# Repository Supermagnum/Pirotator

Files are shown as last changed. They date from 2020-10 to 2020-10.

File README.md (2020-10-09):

# PiRotator #
This is cloned with permission from:
Ville Jussila (wilho / OH8ETB)

This is the rewritten code for raspberrypi based antenna rotator.
See more of project: https://jkry.org/ouluhack/PiRotator

### How do I get set up? ###

* You should get familiar with the code, most things should be pretty selfexplainig
* fill / modify paramaters in the code (pins,ttys, ip:s, speed, etc)
* Try / Error

### Disclaimer ###

 Ville Jussila (wilho / OH8ETB)
 https://jkry.org/ouluhack/pirotator
 
 Free as a free beer or something.. 
 use and do what ever you want, i will be pleased if you mention me on credits.

----------------------------------------------------------------------------
My personal notes and ideas:

It could use:
2X PicoBorg Reverse - Dual 5A Motor Controller ( already supported in the code )

https://www.piborg.org/motor-control-1135/picoborgrev

Or:
Adafruit DC & Stepper Motor Bonnet

https://www.adafruit.com/product/4280

----------------------------------------------------------------------------

1x Ozzmaker BerryGPS-IMU V3 

https://ozzmaker.com/product/berrygps-imu/

----------------------------------------------------------------------------

1X Adafruit LSM6DS33 + LIS3MDL - 9 DoF IMU with Accel / Gyro / Mag

https://www.adafruit.com/product/4485

----------------------------------------------------------------------------

1X Adafruit ADS1115 16-Bit ADC - 4 Channel with Programmable Gain Amplifier

https://thepihut.com/products/adafruit-ads1115-16-bit-adc-4-channel-with-programmable-gain-amplifier

----------------------------------------------------------------------------

Using the BerryGPS-IMU's onboard GPS should permit the raspberry Pi to know its geographic location, that is useful for those who are running mobile setups as that could be used in the calculations of where to point the antennas. It can also detect magnetic north. It will also detect if the mobile setups main mast is not 100% alligned to the "up" or X axis, and can be used to compensate for that if its not perfetcly straight up.
The Adafruit LSM6DS33's IMU can be used to detect the azimuth and elevation of the antennas mounting axle,its movement speed and where it is pointing related to North.

All the part above can communicate using a I2C bus which are supported in the code,in respect to the Borgpi stepper board. Magnetometer and GPS support is apparently not supported in the code.
Neither is "level compensation" .

The suggested features is explained in this picture:

https://github.com/Supermagnum/Pirotator/blob/main/axis.png

-----------------------------------------

It should be possible to supply DC voltages over the Coax cable using:

https://github.com/Supermagnum/Mjollnir

--------

I have made technical drawings for a sturdy aluminium insert that fits a Waterproof ABS box made by Fibox.
Its Product nbr: is 5330372
EAN: 6418074005540
http://www.fibox.com/catalog/135/product/862/5330372_ENG3.html

It has mouting holes for bolts that holds 2X Nema23 Stepper Motors 1.1Nm L56mm 3A + RV30 Worm Reducer gearbox.
Those are frequently found on Ebay, with a nice axle included.
It is to be made of aluminium, aircraft type. Some TIG or MIG welding, drilling of holes and milling is required.

PDF files for manufacturing,with drawings and assembly is located here:

https://github.com/Supermagnum/Pirotator/tree/main/mechanical-hardware

That also includes the Freecad file used to make the drawings.
The adapters that goes on the axles needs to be drilled as you feel fit, and needs a M5 or M6 bolt to stay put on the axle.

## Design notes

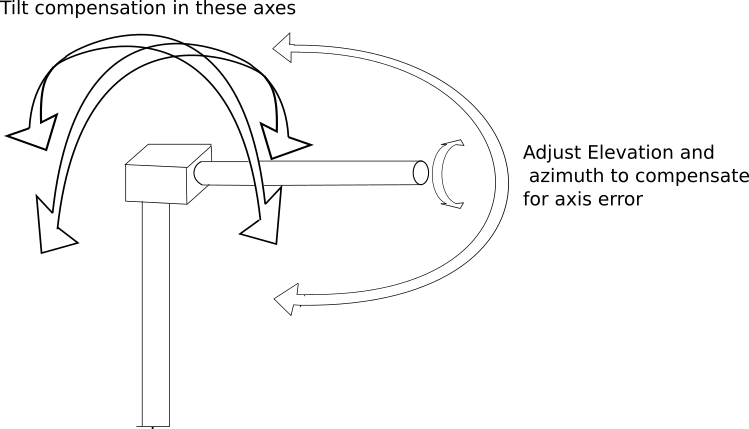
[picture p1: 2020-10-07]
axis.png

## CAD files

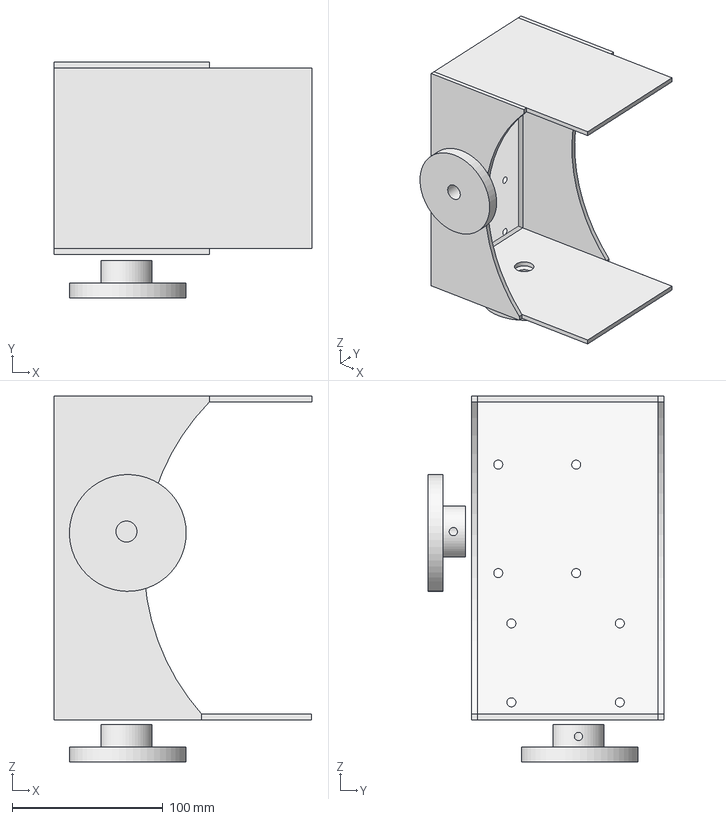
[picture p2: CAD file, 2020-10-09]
mechanical-hardware/az-el-rotor.FCStd
171.1 x 157.0 x 243.0 mm
top-plate
bottom-plate
adapter
sideplate1
sideplate002
back-plate
adapter001

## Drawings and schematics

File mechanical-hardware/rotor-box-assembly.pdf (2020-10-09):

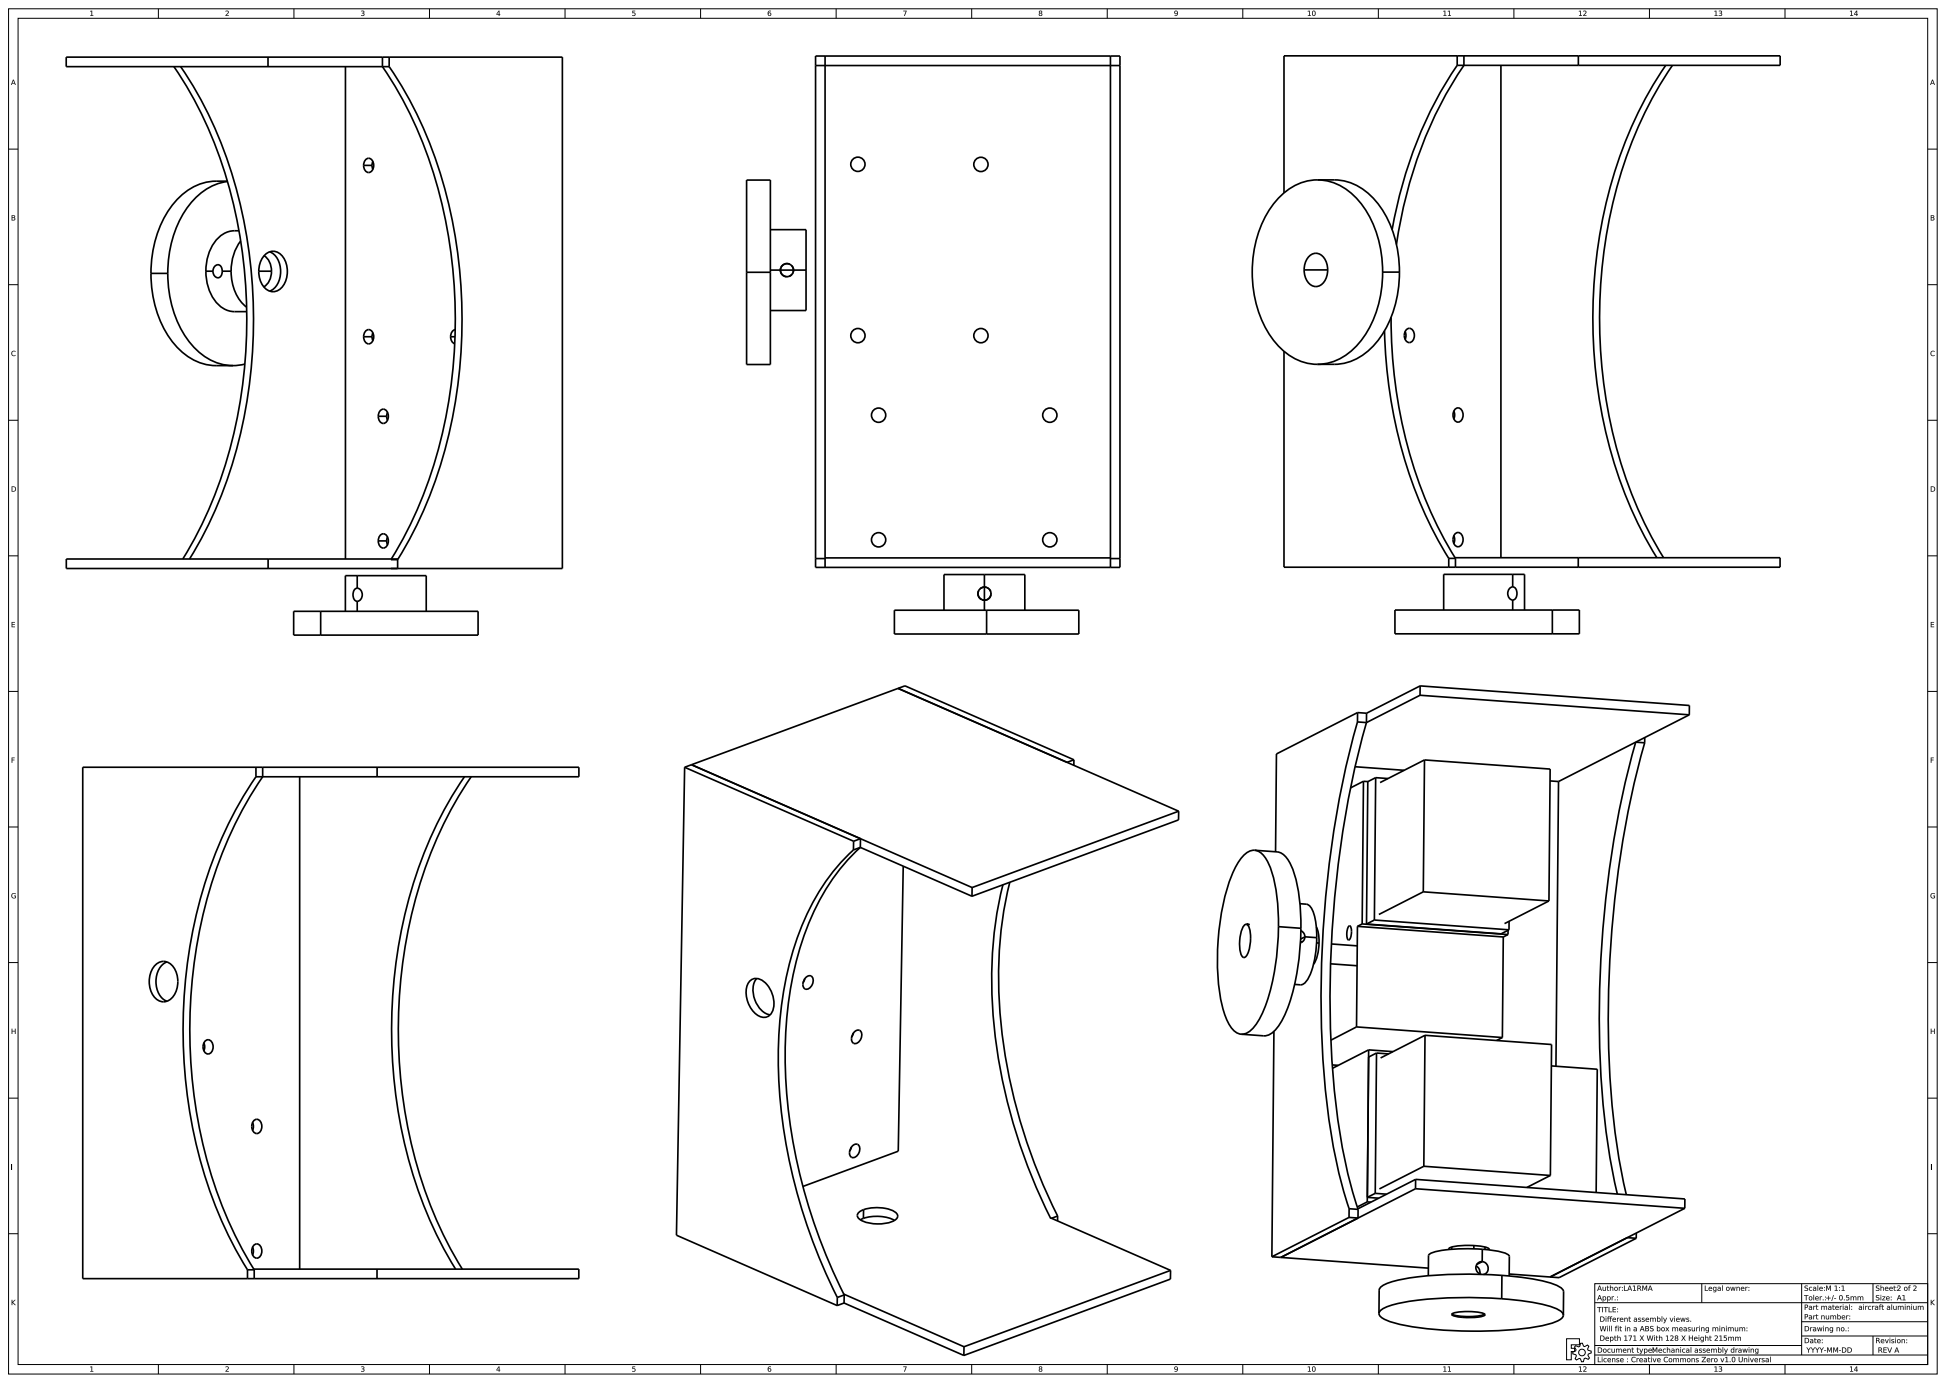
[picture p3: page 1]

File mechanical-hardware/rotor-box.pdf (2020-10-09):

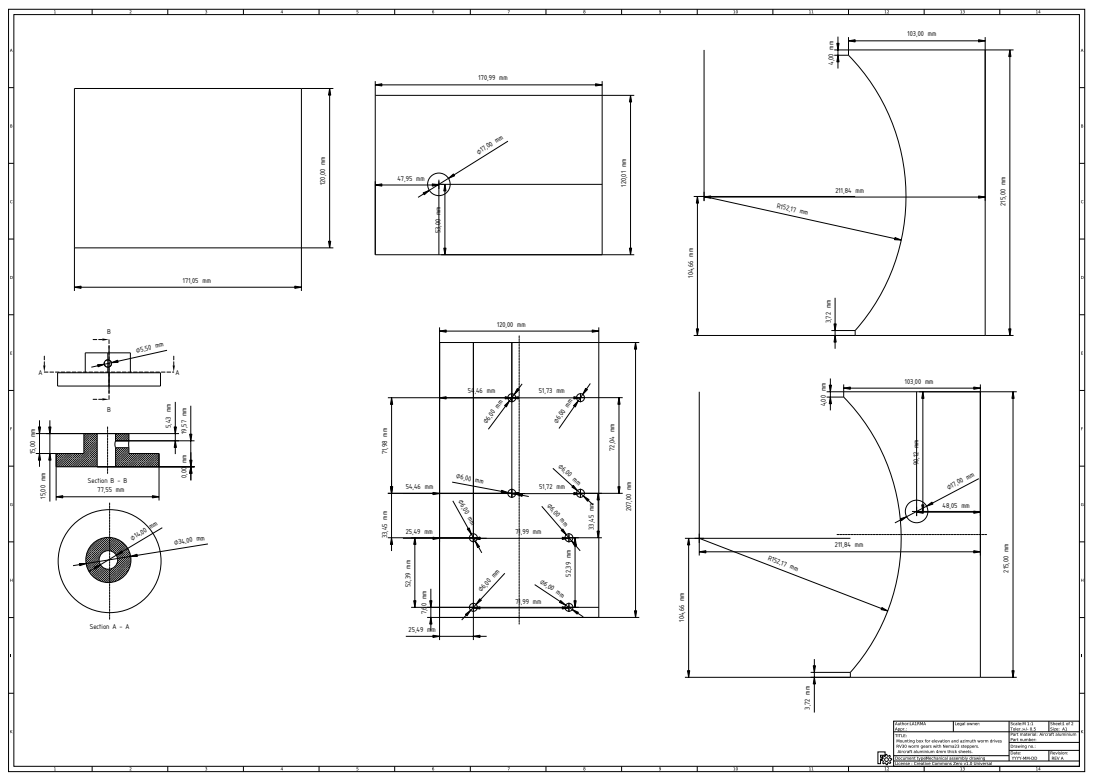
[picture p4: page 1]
ectio

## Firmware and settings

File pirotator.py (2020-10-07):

#!/usr/bin/env python
# coding: latin-1

# pirotator
# Ville Jussila (wilho / OH8ETB)
# https://jkry.org/ouluhack/pirotator
# 
# Free as a free beer or something.. 
# use and do what ever you want, i will be pleased if you mention me on credits.
#
#
#

#General TODO:

# Import library functions we need
#import PicoBorgRev
import time
import threading
import Queue
import Adafruit_BBIO.GPIO as GPIO
import Adafruit_BBIO.ADC as ADC
#import Adafruit_BBIO.UART as UART
##import RPi.GPIO as GPIO
import binstr
import socket
import sys,getopt
import os.path
import math
import serial
import logging
import datetime
import sys
#setup logging
logFormatter = logging.Formatter("%(asctime)s [%(threadName)-12.12s] [%(levelname)-5.5s]  %(message)s")
rootLogger = logging.getLogger()

fileHandler = logging.FileHandler("pirotator.log")
fileHandler.setFormatter(logFormatter)
rootLogger.addHandler(fileHandler)

consoleHandler = logging.StreamHandler()
consoleHandler.setFormatter(logFormatter)
rootLogger.addHandler(consoleHandler)

#rootLogger.setLevel(logging.INFO)
#rootLogger.setLevel(logging.DEBUG)
rootLogger.setLevel(logging.INFO)

#parse args (is this needed?)

#failsafe failsafe based on previous experience
EMERGENCYSTOP = False

#things we need to init everything
azi2c = 11
eli2c = 10


#stepperctrl1  = ["P9_12","P9_15","P9_23","P9_41"]
#stepperctrl1_other = ["P9_23","P9_12","P9_15","P9_41"]
#stepperctrl2 = ["P9_25","P9_27","P9_30","P8_26"]
##GPIO.setmode(GPIO.BCM)
##stepperctrl1 = [27,17,22,24]
#stepperctrl1 = [27,22,17,23]
##stepperctrl2 = [10,9,11,18]
pins = [7,5,6,12,13,19,16,26,20,21]

tty = '/dev/ttyAMA0'
#pins = [26,24,7,22,18,16,15,13,12,11]
#pins = ["P8_17","P8_16","P8_15","P8_14","P8_12","P8_11","P8_10","P8_9","P8_8","P8_7"]

## pseudo code planing for rewrite

#class for handling potentiometer, and filter data from it
class Potentiometer:
    def __init__(self,pins):
        import Adafruit_BBIO.ADC as ADC
        ADC.setup()
        self.pins = pins
        self.deg = 0
        self.filt_deg = 0
        self.ratio = (370.0) #turnrate of the potentiometer
        self.offset = 0.0
        #self.initGPIO(self.pins)
        self.start() #start loop

    def start(self):
        loop = threading.Thread(target=self.loop)
        loop.daemon = True
        loop.start()

    def loop(self):
        values = [] #this is for some averaging
        self.filt_deg = self.read_value()
        self.deg = self.read_value()
        while True:
            value = self.read_value()
            #print value
            #print str(self.deg-10) +" "+ str(value)+" "+str(self.deg+10)
            if self.filt_deg-10 <= value <=self.filt_deg+10: # some filtering if RF causes problems
                self.deg = value
                values.append(value)
                self.filt_deg = sum(values) / float(len(values)) # averaging
                if len(values) > 10:
                    values.pop(0)
                #print len(values)
            else:
                logging.info( "value has been changed too much for 0.1sec, RF-spike?")
            time.sleep(0.1)


    def read_value(self):
        return (self.readGPIO(self.pins)-self.offset)*self.ratio

    def get_value(self):
        return self.filt_deg

    #this does actual reading of the pins
    def readGPIO(self,pins):
        potVal=ADC.read(pins[0])
        potVolt=potVal*1.8
        #debug
        #print "The heading  is: ",potVal*self.ratio, "degrees      (",potVolt,"volts)"
        return potVal



#class for handling rotary encoder, and filter data from it
class RotaryEnc:
    def __init__(self,pins):
        self.pins = pins
        self.deg = 0
        self.filt_deg = 0
        self.ratio = (360.0/1024) #1024 (10bit) for 360 degres
        self.initGPIO(self.pins)
        self.start() #start loop

    def start(self):
        loop = threading.Thread(target=self.loop)
        loop.daemon = True
        loop.start()

    def loop(self):
        values = [] #this is for some averaging
        self.filt_deg = self.read_value()
        self.deg = self.read_value()
        while True:
            value = self.read_value()
            #print value
            #print str(self.deg-10) +" "+ str(value)+" "+str(self.deg+10)
            if self.filt_deg-10 <= value <=self.filt_deg+10: # some filtering if RF causes problems
                self.deg = value
                values.append(value)
                self.filt_deg = sum(values) / float(len(values)) # averaging
                if len(values) > 10:
                    values.pop(0)
                #print len(values)
            else:
                logging.info( "value has been changed too much for 0.1sec, RF-spike?")
            time.sleep(0.1)
 

    def read_value(self): 
        return self.readGPIO(self.pins)[0]*self.ratio
    

    def get_value(self):
        return self.filt_deg

    def initGPIO(self,pins):
        #GPIO.setmode(GPIO.BOARD)
        for pin in pins:
            print pin
            GPIO.setup(pin, GPIO.IN, pull_up_down=GPIO.PUD_UP)
            time.sleep(0.1)

    #this does actual reading of the pins
    def readGPIO(self,pins):
        GPIO.setmode(GPIO.BCM)
        #for pin in pins:
        #    GPIO.setup(pin, GPIO.IN, pull_up_down=GPIO.PUD_UP)
        #    time.sleep(0.001)
        raw = ""
        inv_raw = ""
        for pin in pins:
        #    print pin
            raw += str(GPIO.input(pin))
            time.sleep(0.001)
        for bit in raw:
            if bit == "1":
                inv_raw += "0"
            else:
                inv_raw += "1"
        #print raw
        #GPIO.cleanup()
        return int(binstr.b_gray_to_bin(inv_raw, "big"),2),raw

#class for handling SolidState "encode" via tty
class SSE:
    def __init__(self,tty='/dev/ttyAMA0'):
        self.tty = tty
        print tty
        self.deg = 0
        self.filt_deg = 0
        self.ser = serial.Serial(port=self.tty,baudrate=38400,parity=serial.PARITY_NONE,stopbits=serial.STOPBITS_ONE,bytesize=serial.EIGHTBITS)
        
        self.start() #starts actual loop in own thread
    
    def start(self):
        loop = threading.Thread(target=self.loop)
        loop.daemon = True
        loop.start()

    def loop(self):
        values = [] #this is for making some averaging
        self.filt_deg = self.read_value()
        while True:
            value = self.read_value()

            if self.filt_deg-300 <= value <=self.filt_deg+300: # some filtering if RF causes problems
                self.deg = value
                values.append(value)
                self.filt_deg = sum(values) / float(len(values)) # averaging
                if len(values) > 6: #change this if need more filtering
                    values.pop(0)
            else:
                logging.info( "value has been changed too much for 0.1sec, RF-spike?")
            time.sleep(0.1)

    #this does actual reading from tty
    def read_value(self):
        self.ser.isOpen() 
        self.ser.write("get-360") #+ '\r\n')
        #print "writing get-360"
        out = ''
        # let's wait one second before reading output (let's give device time to answer)
        time.sleep(0.5)
        while self.ser.inWaiting() > 0:
            out += self.ser.read(1)

        if out != '':
            #print ">>" + out
            try:
                return float(out)*-1 # hack, if you mount sensor wrongside up, you dummy!
            except:
                return 0.0
        else:
            print "did not manage to get reading from sensor!"    
            return None

    def get_value(self):
        return self.filt_deg

class relayMotor:
    def __init__(self,pins):
        global EMERGENCYSTOP
        self.hasRelay     = True
        self.relayState   = 0
        self.leftPin    = pins[0]
        self.rightPin     = pins[1]
        print self.leftPin
        print self.rightPin
        #self.power = power
        self.power = False
        self.pulseState = 0
        self.prevdir = -1
        self.setup()
    def setup(self):
        #GPIO.setmode(GPIO.BOARD)
        print "Init LeftPin"
        GPIO.setup(self.leftPin,    GPIO.OUT, initial=GPIO.LOW)
        GPIO.output(self.leftPin, 0)
        print "init RightPin"
        GPIO.setup(self.rightPin,    GPIO.OUT, initial=GPIO.LOW)
        GPIO.output(self.rightPin, 0)
        #print "disable relay"
        #self.toggle_relay(0)
        time.sleep(1)
        print "enable relay"
        self.toggle_relay(1)
        return

    def toggle_relay(self,state=1):
        print "changing motor state to "+str(state)
        self.relayState = state
        #GPIO.output(self.relayPin, state)
        #time.sleep(0.5)
        if state == 0 :
            #GPIO.output(self.enablePin, 0)
            self.power = False
            GPIO.output(self.leftPin, 0)
            GPIO.output(self.rightPin, 0)
            self.prevdir = -1
            #GPIO.output(self.relayPin, 1)
            #time.sleep(0.1)
            #GPIO.output(self.relayPin, 0)

    def power_off(self):
        GPIO.output(self.leftPin, 0)
        self.power = False
        GPIO.output(self.rightPin, 0)
        print "disable motor"

    def do_step(self,dir):

        if EMERGENCYSTOP:  #failsafe
            print "STOPPED BY EMERGENCY STOP"
            return False

        if self.power != True:
            if self.relayState == 0:
                self.toggle_relay(1)
            #GPIO.output(self.enablePin, 0)
            self.power = True
            print "enable motor"
        #GPIO.output(self.enablePin, 0)
        #do step forward
        if dir > 0:
            if self.prevdir != dir:
                print "change dir"
                GPIO.output(self.leftPin, 0)
                GPIO.output(self.rightPin, 0)
                time.sleep(0.5)
                #GPIO.output(self.directionPin, 1)
                #time.sleep(0.5)
                #GPIO.output(self.enablePin, 0)
         #   GPIO.output(self.directionPin, 1)
            self.pulseState += 1
            #GPIO.output(self.pulsePin, self.pulseState % 2)
            GPIO.output(self.rightPin, 1)
        #and to another dir
        else:
            if self.prevdir != dir:
                print "change dir"
                GPIO.output(self.leftPin, 0)
                GPIO.output(self.rightPin, 0)
                time.sleep(0.5)
                #GPIO.output(self.directionPin, 0)
                #time.sleep(0.5)
                #GPIO.output(self.enablePin, 0)
            #GPIO.output(self.directionPin, 0)
            self.pulseState += 1
            #GPIO.output(self.pulsePin, self.pulseState % 2)
            GPIO.output(self.leftPin, 1)
        self.pulseState %= 2
        self.prevdir = dir

        return True

class Stepper:
    def __init__(self,pins):
        global EMERGENCYSTOP
#        self.enablePin    = "P9_12" # Note enable is active low!
#        self.pulsePin     = "P9_15"
#        self.directionPin = "P9_23"
#        self.enablePin    = "P9_25" # Note enable is active low!
#        self.pulsePin     = "P9_27"
#        self.directionPin = "P9_30"

#        self.enablePin    = "P9_23" # Note enable is active low!
#        self.pulsePin     = "P9_12"
#        self.directionPin = "P9_15"
        self.hasRelay     = True
        self.relayState   = 0
        self.enablePin    = pins[0] 
        self.pulsePin     = pins[1]
        self.directionPin = pins[2]
        self.relayPin     = pins[3]

        self.pulseState = 0
        #self.power = power
        self.power = False
        self.pulseState = 0
        self.prevdir = -1
        self.setup()

    def setup(self):
        #GPIO.setmode(GPIO.BOARD)
        print "powering up stepper via relay"
        GPIO.setup(self.relayPin,    GPIO.OUT, initial=GPIO.LOW)
        print "init EnablePin"
        GPIO.setup(self.enablePin,    GPIO.OUT, initial=GPIO.LOW)
        print "init DirectionPin"
        GPIO.setup(self.directionPin, GPIO.OUT, initial=GPIO.LOW)
        print "init PulsePin"
        GPIO.setup(self.pulsePin,     GPIO.OUT, initial=GPIO.LOW)
        print "disable relay"
        self.toggle_relay(0)
        time.sleep(1)
        print "enable relay"
        self.toggle_relay(1)
        GPIO.output(self.directionPin, 0)
        GPIO.output(self.enablePin, 1)
        return

    def toggle_relay(self,state=1):
        print "changing relay state to "+str(state)
        self.relayState = state
        GPIO.output(self.relayPin, state)
        time.sleep(0.5)
        if state == 0 :
            #GPIO.output(self.enablePin, 0)
            self.power = False
            GPIO.output(self.enablePin, 0)
            GPIO.output(self.directionPin, 0)
            GPIO.output(self.pulsePin, 0)
            self.prevdir = -1
            #GPIO.output(self.relayPin, 1)
            #time.sleep(0.1)
            #GPIO.output(self.relayPin, 0)

    def power_off(self):
        GPIO.output(self.enablePin, 1)
        self.power = False
        GPIO.output(self.pulsePin, 0)
        print "disable stepper"

    def do_step(self,dir):

        if EMERGENCYSTOP:  #failsafe
            print "STOPPED BY EMERGENCY STOP"
            return False

        if self.power != True:
            if self.relayState == 0:
                self.toggle_relay(1)
            GPIO.output(self.enablePin, 0)
            self.power = True
            print "enable stepper"
        #GPIO.output(self.enablePin, 0)
        #do step forward
        if dir > 0:
            if self.prevdir != dir:
                print "change dir"
                GPIO.output(self.enablePin, 1)
                GPIO.output(self.pulsePin, 0)
                time.sleep(0.5)
                GPIO.output(self.directionPin, 1)
                time.sleep(0.5)
                GPIO.output(self.enablePin, 0)
         #   GPIO.output(self.directionPin, 1)
            self.pulseState += 1
            GPIO.output(self.pulsePin, self.pulseState % 2)
        #and to another dir
        else:
            if self.prevdir != dir:
                print "change dir"
                GPIO.output(self.enablePin, 1)
                GPIO.output(self.pulsePin, 0)
                time.sleep(0.5)
                GPIO.output(self.directionPin, 0)
                time.sleep(0.5)
                GPIO.output(self.enablePin, 0)
            #GPIO.output(self.directionPin, 0)
            self.pulseState += 1
            GPIO.output(self.pulsePin, self.pulseState % 2)

        self.pulseState %= 2
        self.prevdir = dir

        return True

#yes, after all we do need class for stepper (it is easier to implement to use of other controllers)
# there is no fancy loops or nothing, only .step(direction) for moving stepper one step by step
# should be quite easy to implement on "real" controllers

class Stepper_pico:
    def __init__(self,i2c,power=0.29):
        global EMERGENCYSTOP
        self.i2c = i2c
        self.power = power
        self.sequence = [[self.power, self.power], [self.power, -1*self.power], [-1*self.power, -1*self.power], [-1*self.power, self.power]]
        self.PBR = PicoBorgRev.PicoBorgRev()
        self.PBR.i2cAddress = i2c
        self.PBR.Init()
        self.PBR.ResetEpo()
        self.PBR.MotorsOff()
        self.power = False
        self.step = -1
        self.hasRelay     = False

    def power_off(self):
        self.PBR.MotorsOff()
        self.power = False
        self.step = -1

    def reset(self):
        self.step = -1

    def do_step(self,dir):

        if EMERGENCYSTOP:  #failsafe
            print "STOPPED BY EMERGENCY STOP"
            return False

        self.power = True
        if self.step == -1:
            drive = self.sequence[-1]
            self.PBR.SetMotor1(drive[0])
            self.PBR.SetMotor2(drive[1])
            self.step = 0
        else:
            self.step += dir

        # Wrap step when we reach the end of the sequence
        if self.step < 0:
            self.step = len(self.sequence) - 1
        elif self.step >= len(self.sequence):
            self.step = 0

        # For this step set the required drive values
        if self.step < len(self.sequence):
            drive = self.sequence[self.step]
            self.PBR.SetMotor1(drive[0])
            self.PBR.SetMotor2(drive[1])
        return True
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

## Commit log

2020-10-07 cleaned up some spelling errors.
    [pirotator.py]
2020-10-09 Added a nice metal frame
    Added a nice metal frame for mounting NEMA 23 steppers and RV30 worm gear boxes.
    [az-el-rotor.FCStd]
